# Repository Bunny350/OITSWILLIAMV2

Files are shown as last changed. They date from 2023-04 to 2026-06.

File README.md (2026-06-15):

<p align=center>
    <a>
        <picture>
  <source media="(prefers-color-scheme: dark)" srcset="https://raw.githubusercontent.com/Bunny350/OitswilliamV2/main/Media/Logo/2026/oitswilliamv2-2026-white-text-dark-bg.svg">
  <source media="(prefers-color-scheme: light)" srcset="https://raw.githubusercontent.com/Bunny350/OitswilliamV2/main/Media/Logo/2026/oitswilliamv2-2026.svg">
  OitswilliamV2
</picture>
    </a>
</p>

Welcome to the distant future.

# OitswilliamV2

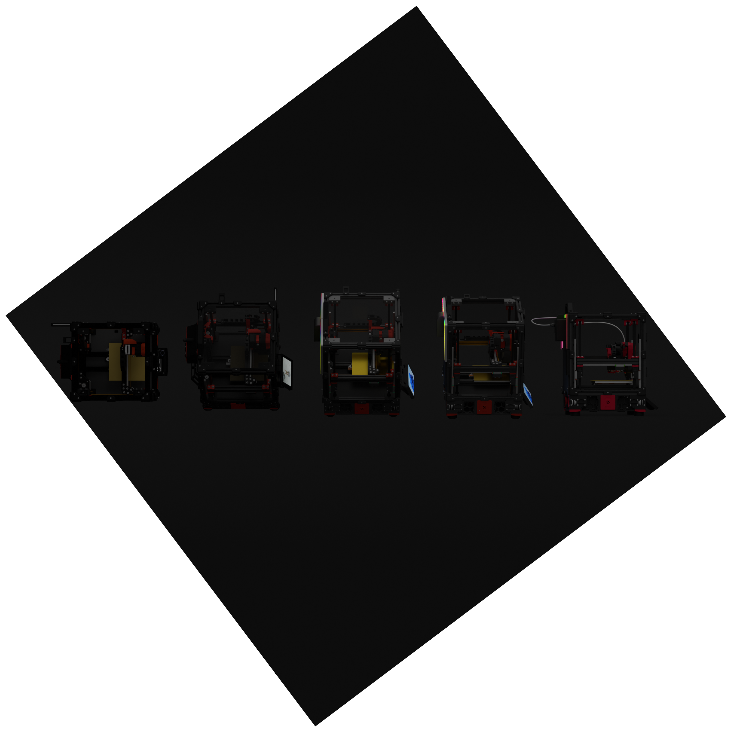
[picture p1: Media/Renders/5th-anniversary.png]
Various iterations of shrunk-down Voron 2 + OitswilliamV2 add-ons.


* Currently featured in V2.3347[^config-on-other-side]!

[View BOM](https://docs.google.com/spreadsheets/d/1hI7gKyXv_dqwRoAh5GxhNzBPyU9dn64bGJ1oHiKoa74/edit?usp=sharing)

OitswilliamV2 is a Voron 2 mod project with unique features, and sometimes breakthrough or stupidly insane features you will stop regretting slowly. It is modded by Oitswilliam Pang and the [original design](https://github.com/VoronDesign/Voron-2) is by the members of Voron Design.

This project is for those who already had a normal and big Voron printer (can be from friends or relatives), with the exception of original parts and skirts.

## Goal
The goal for this mod is:
* Make it unified,
* Make it safer to use,
* And make it intuitive for years to come.

## Feature development status

| Feature  | Status |
| --- | --- |
| Exhaust Lite Generation 2 | Released |
| RealEstate Generation 2 | Released |
| Tracker mount / AirTag mount G4 | Released |
| Tracker mount / Galaxy SmartTag2 mount G2 | Released |
| Replacement / 150mm build 60mm fan mount | Released |
| Replacement / Banger speaker skirts | Released |
| Electronics mounts / Replacement skirts made specifically for SBCs | Released |
| Electronics mounts / Replacement skirts made specifically for NUC PCs (12 Pro to 15 Pro) | Released |

## Features
This repository includes V2 150mm, which is basically Voron 2, but smaller. It includes skirts made for such printing dimensions.

### Using OitswilliamV2 Mod components

When using OitswilliamV2 mod components to modify the printer, you can take either one or more with:
* Sleek yet tiltable touchscreen mount called RealEstate.
    * Touch screen support after having OctoScreen / OctoDash (for OctoPrint users) or KlipperScreen (for Moonraker / lightweight WebUI users)
* Full DC input (no AC). (150mm mod only)
* Smaller version of chamber exhaust called Exhaust Lite.
* Zero limits, indefinite possibilities, through NUC.
* Installing Windows / Debian Linux SBC (single-board computer) or NUC requires replacing the display for the better experience.
* Flying colors (RGB LEDs) via Exhaust Lite.
* Webcam from the back facing at the build plate.
* Make the printer trackable through an item tracker.
* Modular vent port to exhaust hose.
* Some mods even extend to Voron Trident. See STLs Readme for explanation.

### Building from start

OitswilliamV2 is a mod for shrunk-down Voron 2.4 with 150x150x130mm build area except that can be a powerhouse of magical flying colors. Other features including:
* It has a DC power input and power output.
* Will have LED bars for users who are interested in putting "flying colors" in back panel.
* Panel clips can be printed in TPU, to prevent scratching on surfaces prone to scratching.

For the repository creator, it is because he originally did not have enough space to put a proper Voron 2.4.

Check out [parts printing Markdown file](https://github.com/Bunny350/OitswilliamV2/blob/For-Voron-2.4/Parts%20printing.md) on what mod parts should be printed based on your preference. It could entertain, or just be a printer.

#### Recommended BOM changes required when compared normal V2.4 with V2.4 150mm:
| Standard V2.4  | V2.4 150mm |
| --- | --- |
| Z chain - IGUS E2-15-10-028-0 Chain | X/Y chain - IGUS E2i-10-10-018-0 Chain |
| Z chain end - IGUS E2-150-10-12PZ Chain Ends | X/Y chain end - IGUS E2-100-10-12PZ Chain Ends |
| 2x SKR 1.3 | 1x BTT Octopus, FYSETC Spider or MKS Monster8 |

* Z chains should be replaced with X/Y chains due to off-distance towards left.
* Stripping 1kg of weight in such small printer requires usage of 4 Clockwork 1 motors (NEMA17 Motor 17HS08-1004S or equivalent) to replace Z axis stepper motors.

#### Recommended BOM changes required when compared normal V2.4 with the mod when build from start:
| Standard V2.4 recommended | V2.4 150mm + OitswilliamV2 Mod Project |
| --- | --- |
| Coroplast panels as bottom, back and Deck panels | Acrylic panels as bottom, back and Deck panels|
| Internal power supply | External / dedicated power supply |
| AC heated bed | 24V DC heated bed |
| AC input | 24V DC input |

## Kit promotion guidelines
If you want to sell the kits of this mod project, please call it "Voron 2.4 with OitswilliamV2 Mod" or related means that mentions Voron 2 and OitswilliamV2. Do not call it "Voron 2.4 enhanced version" or any other means.

## Questions
### How powerful is OitswilliamV2?
It's more powerful than the average home computers, at least on V2.3347. The only thing that's behind is a computer that has RTX 2060 (desktop) / RTX 2070 Mobile GPU and / or 12th generation Intel Core i7 desktop CPU. However that normally doesn't count if the printer's XY axes motors are not running on 48V power.
### Is 150mm an official spec size of Voron 2.4?
No. There are speculative reasons on why 150mm is not the spec size.
1. The spacing of the mounts between themselves needs to be changed, which means, like for example standard size (from 250mm to 350mm) has 150mm spacing between the bed mounts, but on a 150mm Voron 2.4, the bed mount needs to be narrower. Unless you have a router or a bench that can perfectly drill corners, the bed mount holes must be moved narrower in about half in order to make sure it is easily mounted.
2. Another reason is that one of the chain needs to be changed. Instead of using the chain intended for the Z axis, XY chain is used on the Z axis.
### This part is important, does Oitswilliam Pang Terms of Use apply to this project?
No, as it is licensed under the same license as the original Voron 2 project, or GPL-3.0. Oitswilliam Pang ToU does not apply to this repository.
### Can OitswilliamV2 be the first printer?
Despite it looks way too appealing that you could have indefinite possibilities with this machine, it is intended towards tinkerers. Users who are interested doing this should have a larger printer. Unless if fairytale is real, except that could never.

This project still requires the user to know how to build.
### Is this project suggested, built or vibe-designed by generative AI?
No, none at all, and generative AI can get out.

* Some people said with the help of 250mm spec is the best, this project may agree. Although right now most important parts (from the original and from this repo) are compatible and to be printed on a smaller printer, and then some other parts, except the bottom panel, can be printed within a 150mm print volume.

If you have built a shrunk-down or small printer first (i.e. V0, with or no mods, smaller than Spec V1 / VT, V2 or Switchwire, excluding Z height), you may need to build a bigger printer, or **ask someone or service** for your bigger projects.

For any other questions, you can visit [Oitswilliam Pang support](https://oitswilliam.com/support), where you can contact, email or join the groups for the mod packages, or [VORON Design Discord server](https://discord.gg/voron) and [VORON Forum](https://forum.vorondesign.com) on the original elements.

## Special Thanks
* Thanks to [VORON Design](https://github.com/VoronDesign) for the Voron 2 CAD model.
* The NUC decision is vaguely inspired by [NucDeck by CNCDan](https://github.com/dmcke5/NucDeck), Oitswilliam watched the video before his own research and final decision. 

[^config-on-other-side]: The configuration files for the following printers are not included in this repository, only organized, specific and cleaned-up. To get V2.3347's exact configuration files, you must be a follower of Oitswilliam Pang and then get follower-exclusive features through [this form](https://docs.google.com/forms/d/e/1FAIpQLSe9aEM7jyf0lV2PUAgOg0_tz9F7GI91byWFxUzvXsLlXambJA/viewform?usp=header). Other steps are provided from the form.

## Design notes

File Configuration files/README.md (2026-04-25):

# Configuration files
This folder contains mostly Klipper configuration files and non-Klipper configuration files stored in /Non-Klipper folder.

## Requirements for Non-Klipper configuration files
* This requires Adafruit CircuitPython firmware.
* For RealEstate display mount:
    * Please refer to page 44 of [RealEstate G2.1 assembly manual](https://github.com/Bunny350/OITSWILLIAMV2/blob/For-Voron-2.4/Manuals/realestate-generation-2-1-assembly-guide.pdf) on how to use these files.
    * Please refer to page 17 for wiring illustration or page 12 for wiring diagram.

## Other notes
* Only followers of Oitswilliam Pang from Facebook, Instagram and subscribers on YouTube can view and borrow Oitswilliam's printers' (V2.3347) current configurations. This folder holds cleaned-up configurations.

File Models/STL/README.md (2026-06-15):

This folder stores STLS of this project.
## Compatibility
Some of this mod supports both Voron Trident and Voron 2.4. However, this project is intended for Voron 2.4 with a modded spec.
| Mod name | Folder location | Voron Trident | Voron 2.4 |
| --- | --- | --- | ---|
| Exhaust Lite Generation 2 | Exhaust Lite | :heavy_check_mark: Fully supported |  :heavy_check_mark: Fully supported |
| ELG2 LED back | Exhaust Lite/LED Back | 150mm mod spec specific | 150mm mod spec specific |
| RealEstate Generation 2 | RealEstate | :heavy_check_mark: Fully supported | :heavy_check_mark: Fully supported |
| Tracker mount (AirTag and Galaxy SmartTag) | Tracker mount | :heavy_check_mark: Fully supported[^daretodeploy] | :heavy_check_mark: Fully supported[^daretodeploy] |
| Deck mounting brackets[^notea] | Replacement | :heavy_check_mark: Fully supported | :heavy_check_mark: Fully supported |
| Front side of 150mm mod skirt[^noteb] | Replacement/Skirt | :x: Not supported | 150mm mod spec only |
| Fan mounting skirt for 150mm mod[^notec] | Replacement | 150mm mod spec specific | 150mm mod spec specific |
| Bottom panel of the printer | Replacement/Bottom panel | 150mm mod spec specific | 150mm mod spec specific |
| 150mm mod SBC-specific skirt | Electronics mounts/Computer mounting/SBC | :x: Not supported | 150mm mod spec specific |
| 150mm mod NUC-specific skirt[^noted] | Electronics mounts/Computer mounting/NUC | :x: Not supported[^nointents] | 150mm mod spec specific |
| Condensed 60mm fan grill | Replacement | :heavy_check_mark: Fully supported |  :heavy_check_mark: Fully supported |

[^notea]: The part in question is called *din-rail-bypass-deck-mount-X4.stl*. These (being four of these parts) are used to mount the deck panel without the DIN rail being mounted with. It can be mounted with M3x8mm to M3x10mm BHCS / SHCS. This part is located in Replacements folder.
[^noteb]: This includes the following part names: *front-skirt-150mm-mod-left.stl* and *front-skirt-150mm-mod-right.stl*.
[^notec]: This part mounts one 60mm fan or some accessories into the printer. It uses the same mounting screws as the original. There are two variants for attaching the mount into the frame, *[base]150mm-60mm-fan-mount-m3x8.stl* which uses M3x8mm SHCS, but it seemed way too weak, so there is another variant called *[base]150mm-60mm-fan-mount-m3x12.stl* which requires M3x12mm SHCS on mounting to the frame.
[^noted]: Currently supports NUC 12 Pro to 15 Pro, but we have intent to make one that is made for NUC 16 Pro.

* Most mods for Voron 2.4 do support Voron Trident, but some parts need user testing.
* Most mods for Voron 2.4 do not support Voron 0, Voron 1.8, Voron Legacy or Voron Switchwire.

### <div id="nuc">NUC Mini PCs and SBCs</div>

OITSWILLIAMV2 mod now uses ASUS / Intel NUC PC which is inserted onto the back of the printer's skirt. This part only supports V2 in 150mm build size (mod). It used to support Morefine M6 with two mounting options (DIN rail mount or adhesive on the bottom) and universal (variant doesn't matter), but because of it's bad performance and compatibility, we have decided to discontinue them. OITSWILLIAMV2 also contains 150mm (mod) skirts that are made specifically for single-board computers such as Raspberry Pi, et cetera.
* For users who still want or repair mounts for Morefine M6, [the last CAD commit with such model](https://github.com/Bunny350/OITSWILLIAMV2/tree/df8fa697d1fd7cfa57b1f74a1fd6d7f7c9acae59/Models/CAD/VORON2.4-150mm) can still be accessed, and the STL models can be accessed [here](https://github.com/Bunny350/OITSWILLIAMV2/issues/4).

## Color guide
* If the part name does not have any brackets at the beginning you may use the printer's base color to print the part.
* [acc] - Printer accent color.
* [opaque] - Opaque color, it should block most of the glowing elements. It can be opaque base or accent color.
* [transparent] - Transparent color, it should allow the glow to pass-through and can be diffused. Transparent PETG / PC is recommended.
    * Transparent ABS can be used but seems rare in FFF 3D printing.

##  Printing guidelines
This section tells how to basically configure print settings.
Some parts require a bigger printer to print.
### Settings
These parts require ABS, PETG or PC to print.
Settings and parameters must be set to the following values:
* Layer height 0.2mm
* Layer width of 1.6mm (for 0.4mm nozzle) or 4 layer lines (for 0.4 / 0.6mm nozzle)
* Infill density of 40%, but,
    * On LED diffusers ([transparent]led-diffuser-(direction)-100-infill), the infill density must be 100%,
* Any slicers are welcome.
* Some inner parts such as grills requires modifiers to optimize printing performance.

[^daretodeploy]: This is best when showing off people at the 3D printer-related events, to prevent losing the printer. I know about MRRF, but I couldn't visit. Maybe in the near future I may do that.
[^nointents]: There is no intent in extending support to Trident, V0, et cetera, but there will be for Micron Plus.

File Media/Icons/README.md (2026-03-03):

# Icons
These are the icons made specifically for OitswilliamV2. These icons may not be used in assembly guides of their own.

| Icon | Artist |
| --- | --- |
| realestate-g2-display-s.svg | [Oitswilliam Pang](https://github.com/Bunny350) |
| v2-150mm-stealthburner.svg  | [Oitswilliam Pang](https://github.com/Bunny350) |

## Making new icons
Please refer to [2D drawings in Contributing Markdown document](https://github.com/Bunny350/OITSWILLIAMV2/blob/For-Voron-2.4/CONTRIBUTING.md) on making new icons for this project.

The icon must be in SVG, and must be simplified through your imagination.

### Simplification
To simplify the products for icons, it needs to:
* Have text removed,
* No small cutouts,
* Have complex geometries reduced.

## Passing icons to your *own* materials outside OitswilliamV2 project

It is recommended to credit our designs when passing these icons to your own materials. 

You may use the following phrase or related:

* *"Some icons" by "artist" in OitswilliamV2.*

For example, if there are icons *realestate-g2-display-s* and *v2-150mm-stealthburner* used, it will be written as *realestate-g2-display-s and v2-150mm-stealthburner by Oitswilliam Pang in OitswilliamV2.*

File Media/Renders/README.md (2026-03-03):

# Renders folder
This folder holds render images of Voron 2 150mm + OitswilliamV2 mod.

## Don't let generative AI companies train data out of these, thank you. Although it didn't help as these don't read disclaimers, certain licensing terms, certain copyright warnings or general warnings.

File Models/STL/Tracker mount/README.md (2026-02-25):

# Tracker mount
This folder contains tracker mount to Voron printers, for AirTag and Galaxy SmartTag2.
## IMPORTANT NOTE
**Do not use these for unwanted tracking. These parts are only intended to track printers that are installed with them.**

## Recommended materials
These parts are recommended to be printed in **ABS / ASA**. Other materials can be printed but the compliant design may not function properly, including but not limited to, requiring excessive force to secure or remove.

## Installation instructions
Please refer to the [assembly guide for both tracker mounts](https://github.com/Bunny350/OitswilliamV2/tree/For-Voron-2.4/Manuals/TRACKER-MOUNT-2026.pdf) for exact installation.
Insert the tracker to the main unit, then secure it with the bracket or nut. The assembled unit is then attached to the one of the skirt of the printer that has the unit mount installed.

## Removal and deactivation instructions
* Turn the unit counter-clockwise and then pull to remove it.
* For AirTag, unless the part is imperfect, the battery case can be removed without removing the bracket, otherwise, remove the bracket first, by turning the bracket counter-clockwise, and then remove that.
* For Galaxy SmartTag2, a SIM ejector tool is required. It can be made from the paper clip. Turn the nut counter-clockwise to remove it, and then use the SIM ejector tool to punch down in the hole that is placed at the back-middle of the silver ring of the tracker, and pull the battery tray.

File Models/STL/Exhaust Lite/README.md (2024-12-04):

## Directory printing guide for ELG2
This page shows what method you should use when choosing. Directories that are not in list must have all parts printed (excluding another directory in it).

### Legend: Parent / Child / Child / [Variants] ...

### Directories that need all parts in it printed:
* Filter cartridge
* LED Back (opaque visibilities)

### Directories that let you print either part by back panel thickness:

* Body unit / Exhaust spacer
* LED Back / [Back panel thickness (4 / 6mm)]

### Directories that let you print one of either part by back panel thickness and max cabling depth:

* Cable cover / [Back panel thickness (4 / 6mm)] / [Depth (10 / 15mm)]

### Directories that let you print one of either parts by screw type of coupler:

* Bowden coupler
	* Currently, one with runout sensor only supports 1/8" BSPP coupler.

### Directories that let you print one of either part by screw type:

* Unit cover

### Directories that let you print one of either part by whether should you embed a webcam to ELG2:

* Chamber cover

### Directories that let you print for one of either variant of webcam you mount, or not required if not installing it:

* Webcams

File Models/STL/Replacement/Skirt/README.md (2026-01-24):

# The skirt folder

This folder contains skirt parts intended to be placed on V2 in 150mm build volume.

## Side skirts
The side skirts (side_skirt_a_150_mesh.stl and side_skirt_b_150_mesh.stl) needs processing settings changed prior to print:

* Zero top and bottom layers
* 6 wall count, if using 0.4mm nozzle, or 2.4mm walls.
* Sparse infill density can be between 15% and 50%.
* You can choose what infill pattern that fits for you.
* Might as well adjust the infill direction in angle if you are not satisifed during preview before print. 

If the printer is going to be installed with banger speakers, then you may only print a pair, otherwise you may print two pairs.

## Front skirt
The front skirts (front-skirt-150mm-mod-left.stl and front-skirt-150mm-mod-right.stl) can follow the normal print settings, but it does not have any screws to hold, as it might otherwise weaken the part significantly. Because of this, I made a workaround where the front clips are attached to the bottom panel via screws instead of the multi-sided tape.

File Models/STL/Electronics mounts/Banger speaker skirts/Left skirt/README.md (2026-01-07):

This folder consists of two models that must be grouped and "merged".
## Printing guide
The normal part can be printed with the current settings, but the infill modifier must have its settings changed:
* There should not be top or bottom layers, you may set them to 0 / 0mm in both top and bottom layers.
* You may add or deduct one wall layer.
* Infill density must be between 25% to 50%.

## Setup guide on slicers

### UltiMaker Cura (with workaround)
Based of [How to merge and group models in UltiMaker Cura from UltiMaker Support](https://support.makerbot.com/s/article/1667411295122)
* Drop or open the STL models into the plate.
* Select **Merge Models**.
* Lay the model down and position the model to what you want.
* Ungroup the models.
* On the *infill modifier* of the part, modify its top and bottom layers by using **Per-model settings**.
    * Open the options by clicking **Select settings**.
    * Check the **Top/Bottom Thickness**. **Infill Density** and **Infill Pattern** is optional and will depend on what you want.
    * Change the Top/Botom Thickness to 0, and if you like to change the Infill Density, you may set it to somewhere between 25% to 50%, depending on what you want.
* You may do the same for the other part.
* The part can be sliced and printed.

### PrusaSlicer, et cetera, including Bambu Studio
**You must be at least in advanced mode in order to do so.**
* Drop or open either STL or 3MF models, for PrusaSlicer and not BambuStudio, you may open the 3MF model. It must be placing both models in a single drop per folder.
* It will warn that there are multiple parts while trying to load, Choose **Yes** as these are intended so.
* 
**This section is used for PrusaSlicer users if the infill modifier is not ready, or has top / bottom layers.**

Based of [Modifier meshes from Prusa Knowledge Base](https://help.prusa3d.com/article/modifiers_1767#modifier-meshes).
* Select the infill modifier of the part through the object menu, then click the edit cogwheel next to the part name or right-click on the part name.
* It will pop up the menu, select **layers and perimeters**. You can optionally add **infill** as well.
* Change the infill modifier top and bottom layers to 0, perimeter may also be set to 0, if one of the mesh is turned into top or bottom layer.
* You can optionally change the sparse infill density of such part, you may set it somewhere between 25% to 50%, you can also change its infill pattern to something you like, such as honeycomb.

**This section is specific to BambuStudio.**

Based of [Object level parameters from Bambu Lab Wiki](https://wiki.bambulab.com/en/software/bambu-studio/how-to-set-slicing-parameters#object-level-parameters)
* After importing, toggle the process to **objects**.
* Select the mesh modifier *in the process menu*.
* In the strength section for the infill modifier, set both **top shell layers** and **bottom shell layers** to 0.
* You can optionally change the sparse infill density of such part, you may set it somewhere between 25% to 50%, you can also change its infill pattern to something you like, such as honeycomb.

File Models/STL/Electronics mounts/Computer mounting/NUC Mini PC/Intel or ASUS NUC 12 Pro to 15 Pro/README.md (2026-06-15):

This folder consists of necessary parts for mounting ASUS / Intel NUC 12 Pro to 15 Pro into Voron 2 in 150mm mod.

## Requirements
[View BOM, you may select NUC Mini PC when browsing.](https://docs.google.com/spreadsheets/d/1hI7gKyXv_dqwRoAh5GxhNzBPyU9dn64bGJ1oHiKoa74/edit?usp=sharing)

### In a nutshell
* Base color of the printer,
* ASUS / Intel NUC 12 Pro, 13 Pro, 14 Pro or 15 Pro, **slim version**
    * Other versions, including the tall version, *Pro Plus*, *Pro AI* or any other variants do not fit. In addition, these printed parts heavily rely on such models of NUC with the metal shell.

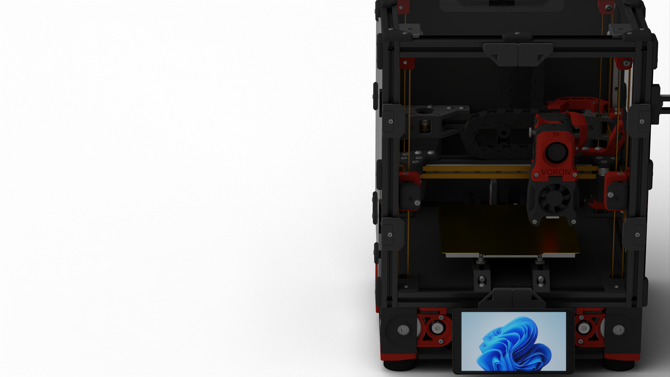
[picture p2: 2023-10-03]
Media/Renders/v2-150mm-top-side-cam-off-righthand-2K.png

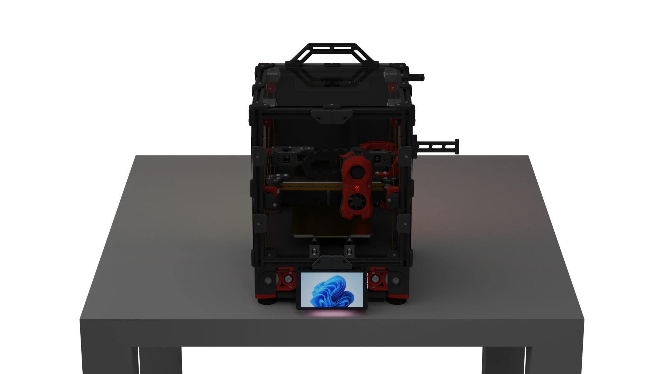
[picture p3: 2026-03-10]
Media/Renders/v2-150mm-oitswilliamv2-mod-top-bottom.png

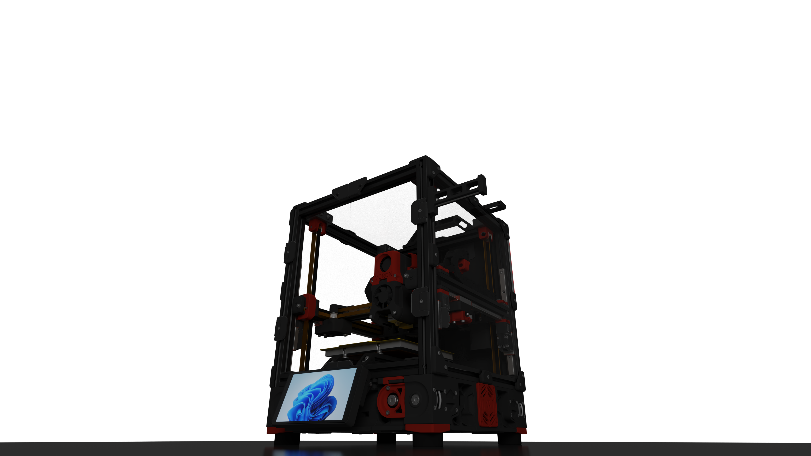
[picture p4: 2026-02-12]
Media/Renders/bottom-front-side-render.png

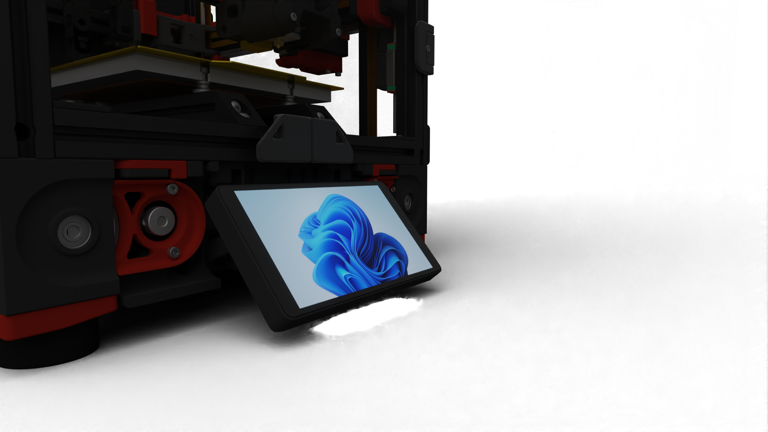
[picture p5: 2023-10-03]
Media/Renders/realestate2-side.png

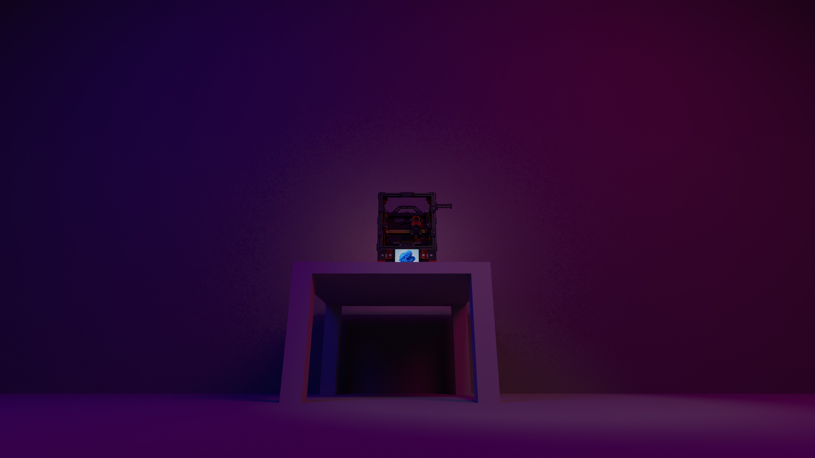
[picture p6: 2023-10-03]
Media/Renders/sick machine-2K.jpg

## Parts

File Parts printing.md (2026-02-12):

# Parts printing
This page guides users on printing required parts.

## I want it to live, entertain everyone, be like a boombox and treat it like a computer
The required parts are:
* RealEstate G2
* NUC-specific skirt
* Banger speakers
* 2x 60mm fan mount for 150mm Voron printers ([STL](https://github.com/Bunny350/OITSWILLIAMV2/tree/For-Voron-2.4/Models/STL/Replacement)) ([CAD](https://github.com/Bunny350/OITSWILLIAMV2/tree/For-Voron-2.4/Models/CAD/VORON2.4-150mm/150mm%20mod%2060mm%20fan%20mount))
* 1 pair of normal side skirts ([STL](https://github.com/Bunny350/OITSWILLIAMV2/tree/For-Voron-2.4/Models/STL/Replacement/Skirt))
* Tracker mounting is generally recommended ([STL](https://github.com/Bunny350/OITSWILLIAMV2/tree/For-Voron-2.4/Models/STL/Tracker%20mount)) ([CAD](https://github.com/Bunny350/OITSWILLIAMV2/tree/For-Voron-2.4/Models/CAD/Tracker%20mount))

## I don't care about making it an enthusiastic computer, I've just want it to print, follow as many components as the original, but small
The required parts are:
* SBC-specific skirt ([STL](https://github.com/Bunny350/OITSWILLIAMV2/tree/For-Voron-2.4/Models/STL/Electronics%20mounts/Computer%20mounting/SBC)) ([CAD](https://github.com/Bunny350/OITSWILLIAMV2/tree/For-Voron-2.4/Models/CAD/VORON2.4-150mm/SBC-specific))
* 2x 60mm fan mount for 150mm Voron printers ([STL](https://github.com/Bunny350/OITSWILLIAMV2/tree/For-Voron-2.4/Models/STL/Replacement)) ([CAD](https://github.com/Bunny350/OITSWILLIAMV2/tree/For-Voron-2.4/Models/CAD/VORON2.4-150mm/150mm%20mod%2060mm%20fan%20mount))
* 2 pairs of normal side skirts ([STL](https://github.com/Bunny350/OITSWILLIAMV2/tree/For-Voron-2.4/Models/STL/Replacement/Skirt))
* Tracker mounting is generally recommended ([STL](https://github.com/Bunny350/OITSWILLIAMV2/tree/For-Voron-2.4/Models/STL/Tracker%20mount)) ([CAD](https://github.com/Bunny350/OITSWILLIAMV2/tree/For-Voron-2.4/Models/CAD/Tracker%20mount))

## Required spares
This mod requires a dedicated / external power supply, of:
* At least 300W for one with NUC inside,
* Or at least 200W for one with SBC.

## Procedure
This mod may intersect with the original assembly manuals: Voron 2 (2.4r2), Stealthburner, Tap. Please check this if you are building from start to finish.

* The mod may not use DIN-based electronics mounting, especially where such may conflict with NUC skirt.
* This mod recommends DC-powered bed, which removes the requirement of solid state relay (SSR).
* Voron 2 assembly manual from start to page 146,
* Voron Stealthburner assembly manual, from start to page 58, if using such tool head,
* Voron Tap assembly manual, if using such upgrade, otherwise proceed from page 59 to 67 of Stealthburner manual (if using such tool head),
* Pages 148 and 149 of Voron 2 assembly manual, 
* OitswilliamV2 NUC skirt, from start to page 25, if using NUC, or original assembly manual from pages 150 to 152 if using SBC,
* Pages 158 to 161 of Voron 2 assembly manual, if not using Voron Tap upgrade,
* Pages 162 to 164 of Voron 2 assembly manual,
* Pages 180 to 209 of Voron 2 assembly manual, AC part may be excempted,
* Pages 210 to 237 of Voron 2 assembly manual,
    * Pages 211, 214 to 216, and 220 to 221 contains monochrome LCD display,
    * If you are switching to RealEstate display, these sections need to be ignored and then referred to OitswilliamV2 RealEstate display assembly manual,
    * Item tracker mounting manual, if installing an item tracker,
    * The skirt mounting part of OitswilliamV2 NUC skirt, from pages 26 to 28, if already using NUC,
* Pages 238 to 249 of Voron 2 assembly manual, if using the original enclosing,
* Pages 250 to the end of Voron 2 assembly manual.

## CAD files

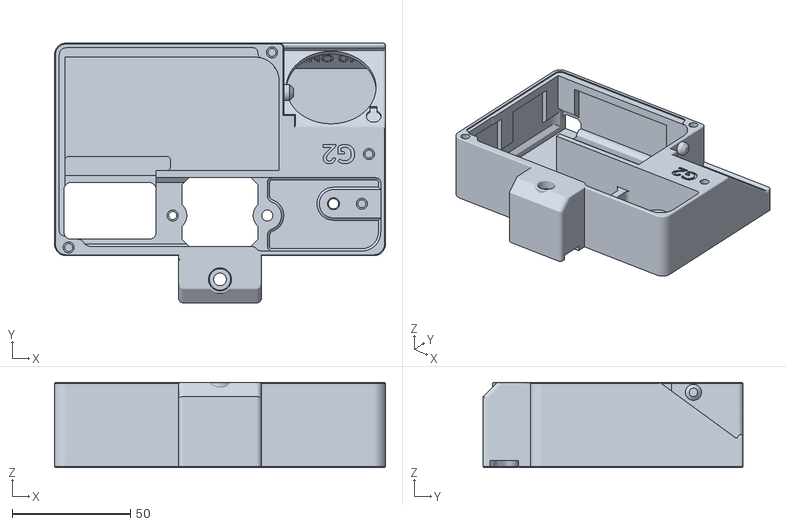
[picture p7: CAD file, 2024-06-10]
Models/STL/Exhaust Lite/Body unit/main-body.stl
140.0 x 110.0 x 36.0

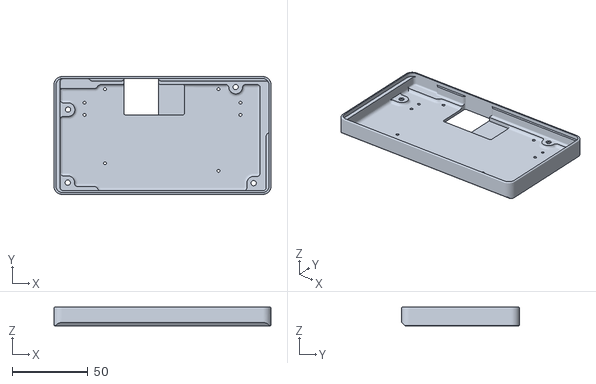
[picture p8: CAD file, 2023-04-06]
Models/STL/RealEstate/Main screen/main-screen-mount-waveshare-5.5-inch-amoled.stl
143.4 x 77.8 x 12.4

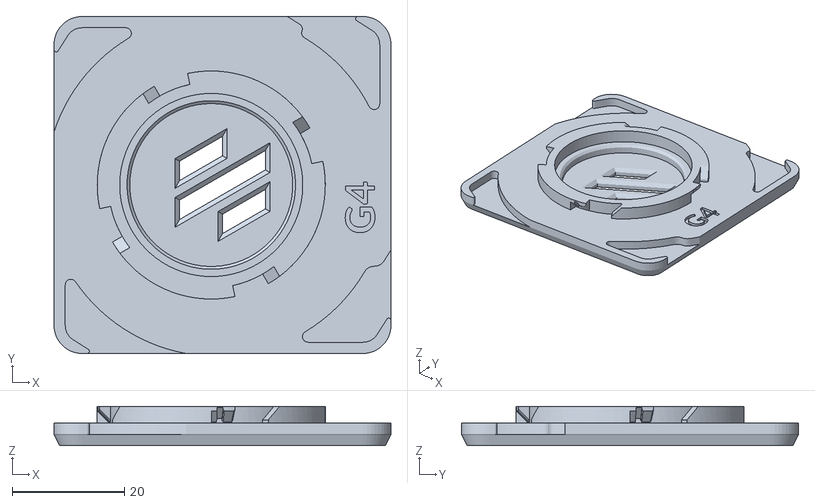
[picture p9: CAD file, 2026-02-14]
Models/STL/Tracker mount/AirTag/[acc]tracket-mount-airtag-main-g4.stl
60.0 x 60.0 x 7.00

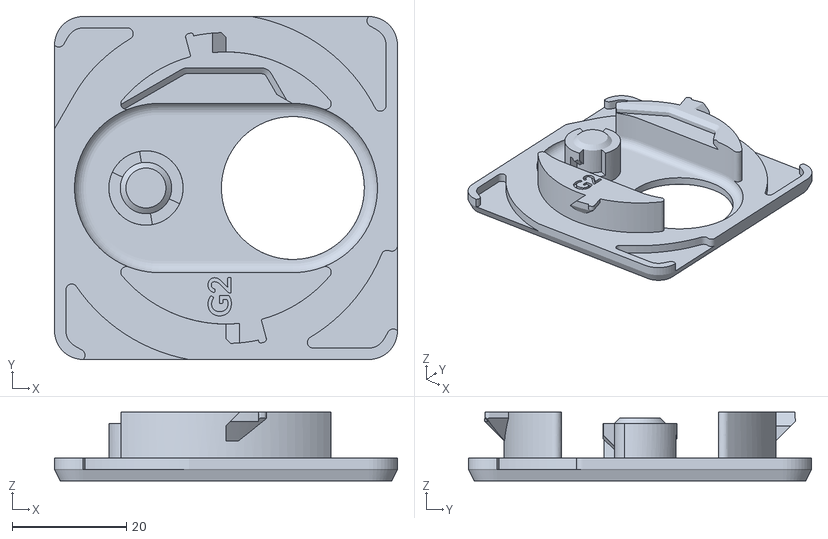
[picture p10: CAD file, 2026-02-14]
Models/STL/Tracker mount/Galaxy SmartTag2/[acc]tracket-mount-smarttag-main-g2.stl
60.0 x 60.0 x 12.0

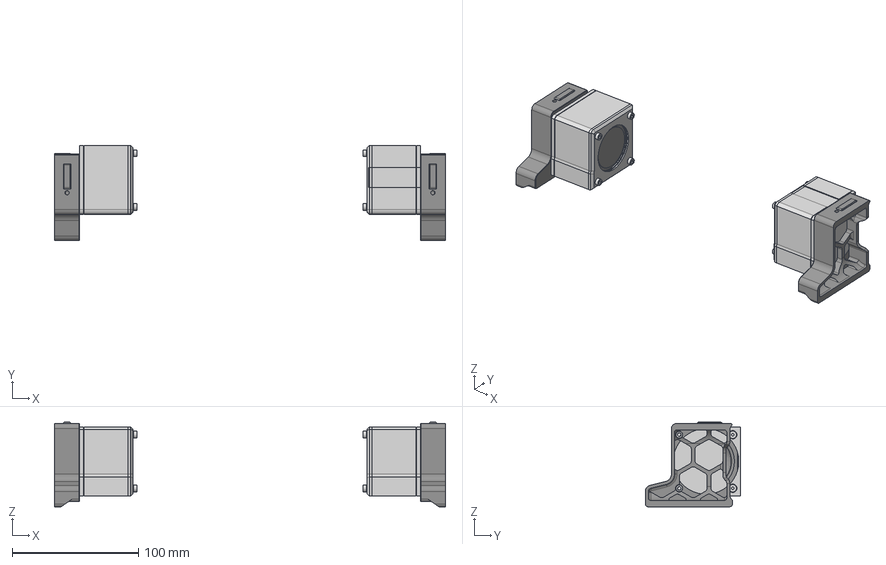
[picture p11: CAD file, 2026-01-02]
Models/CAD/Banger speaker skirts/banger speaker skirts on v2.step
310.0 x 75.6 x 67.0 mm
left side skirt infill mesh modifier
side_skirt_150_speaker_left
speaker unit
M3x6 FHCS v1 x 2
M3x8 SHCS x 6
M3 Threaded Insert x 8
right side skirt infill mesh modifier(Mirror)
side_skirt_150_speaker_right
speaker unit(Mirror)
M3x6 FHCS v1_1 x 2
M3x8 SHCS(Mirror) x 6
M3 Threaded Insert(Mirror) x 8

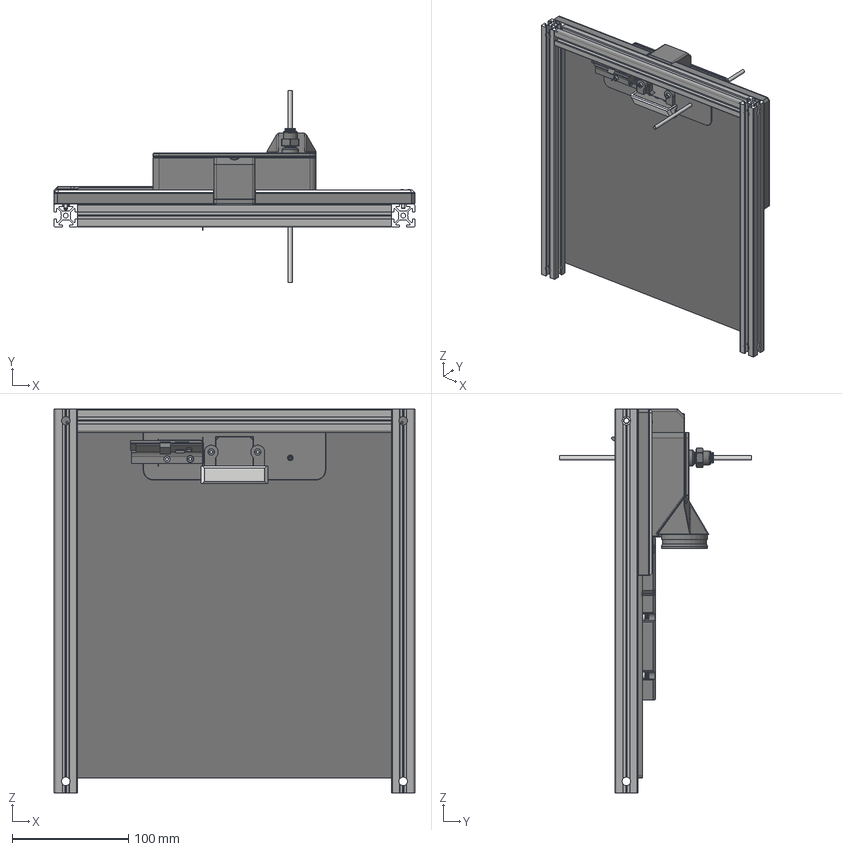
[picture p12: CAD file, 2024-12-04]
Models/CAD/Exhaust Lite/exhaust-lite-gen2 v40.step
310.0 x 165.4 x 330.1 mm
M2x10 Self-tapping Screw (3) x 12
led strip (READ MANUAL FOR QUANTITY)
M3x6 BHCS x 14
diffuser-6mm
ov5640-mount-back
ov5640-front-face
M3x8 SHCS (15) x 4
mini-webcam-backside
mini-webcam-cover
hardware (4)
exhaust-lite-chamber-cover-webcam
M3 Threaded Insert (69) x 9
cover-shcs
cover-bhcs
main-body
M3x20 SHCS (15)
M5x40 SHCS (5)
filter pieces
BSP Bowden Connector v1 (1)
pc4-m6-adapter
8-1-bspp-adap-runout
MR85 Bearing x 2
Omron D2F Microswitch
M5x30 BHCS (4)
filament dummy
40x40x10 DC Fan
6x3 magnet (1)
exhaust-lite-chamber-cover
M3x8 SHCS x 2
6x3 magnet
M3x16 SHCS (4) x 2
led strip (READ MANUAL FOR QUANTITY) (1)
M3x10 FHCS (5) x 2
spliced bowden tube

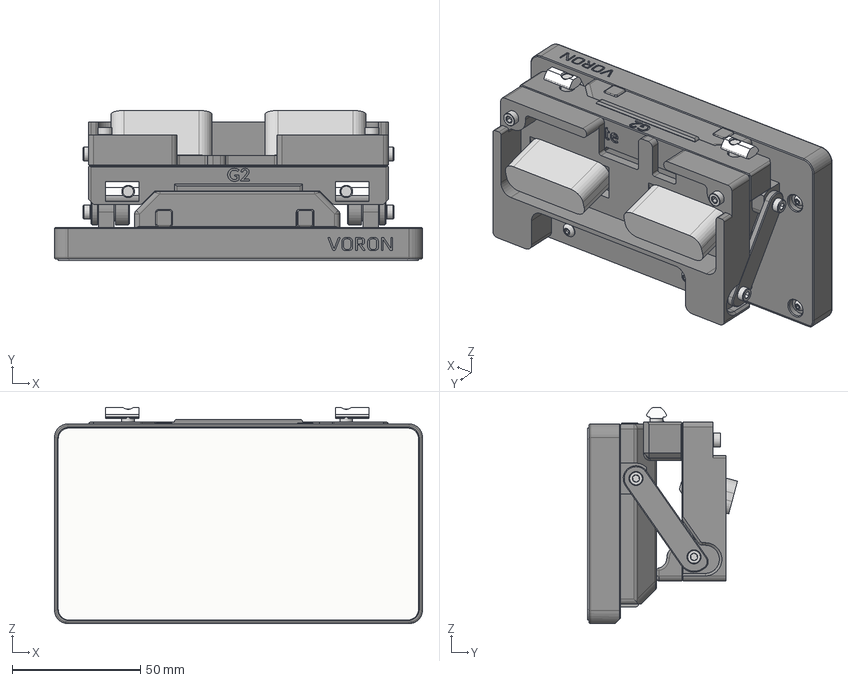
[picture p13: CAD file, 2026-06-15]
Models/CAD/RealEstate/realestate 2.step
143.4 x 58.5 x 84.3 mm
glass front
main display panel
92095A456_NO THREADS x 4
KW10 Microswitch (3)
hatch
hardware
hardware (1)
94180A331_NO THREADS_Tapered Heat-Set Inserts for Plastic x 4
91292A114_18-8 Stainless Steel Socket Head Screw(Mirror) x 2
94180A331_NO THREADS_Tapered Heat-Set Inserts for Plastic(Mirror) x 2
91292A114_18-8 Stainless Steel Socket Head Screw x 2
teflon-tube x 2
94209A315_NO THREADS x 8
6x3mm magnets x 2
92095A179_NO THREADS x 6
91290A120_NO THREADS_Alloy Steel Socket Head Screw x 2
M5x10 BHCS (15) x 2
2020 Drop-in T-nut, M5 (10) x 2

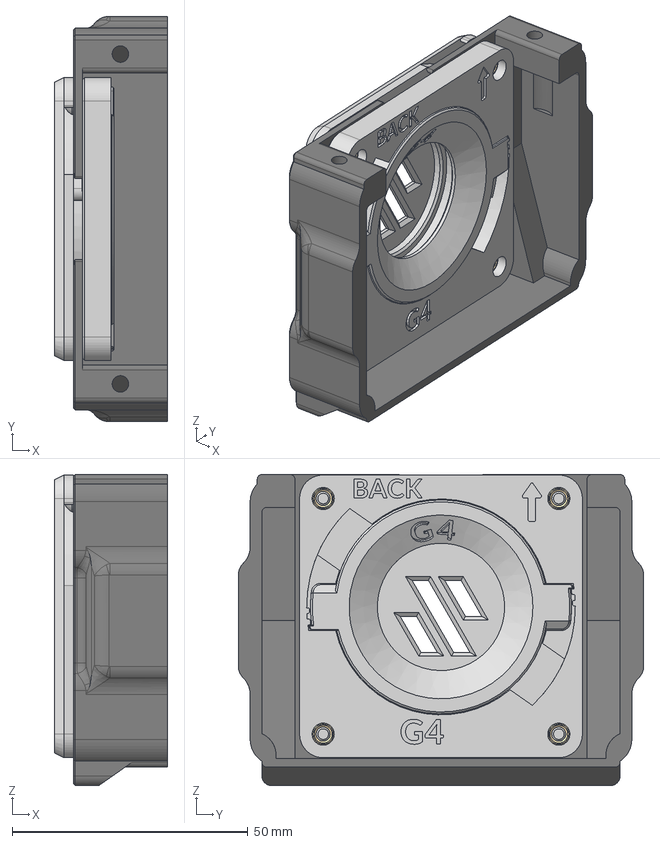
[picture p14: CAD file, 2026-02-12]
Models/CAD/Tracker mount/AirTag/oitswilliamv2 2.4r2 tracker mount (airtag) g4.step
24.0 x 86.0 x 66.0 mm
main
97763A812_NO THREADS_18-8 Stainless Steel Button Head Hex Drive Screw s x 4
M3 Threaded Insert x 4
reference materials

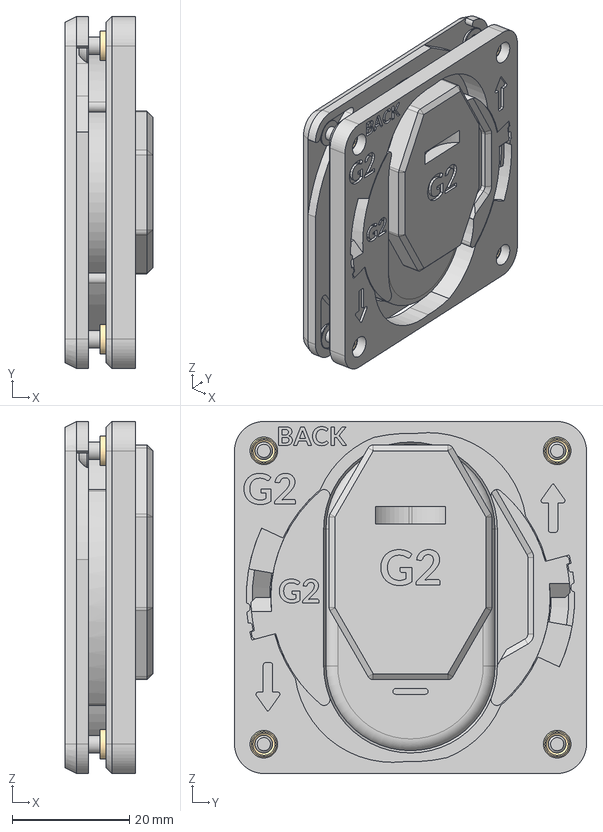
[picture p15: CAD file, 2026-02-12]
Models/CAD/Tracker mount/Galaxy SmartTag2/oitswilliamv2 2.4r2 tracker mount (smarttag) g2.step
15.0 x 60.0 x 60.0 mm
main
[raw]tracker
97763A812_NO THREADS_18-8 Stainless Steel Button Head Hex Drive Screw s x 4
M3 Threaded Insert x 4

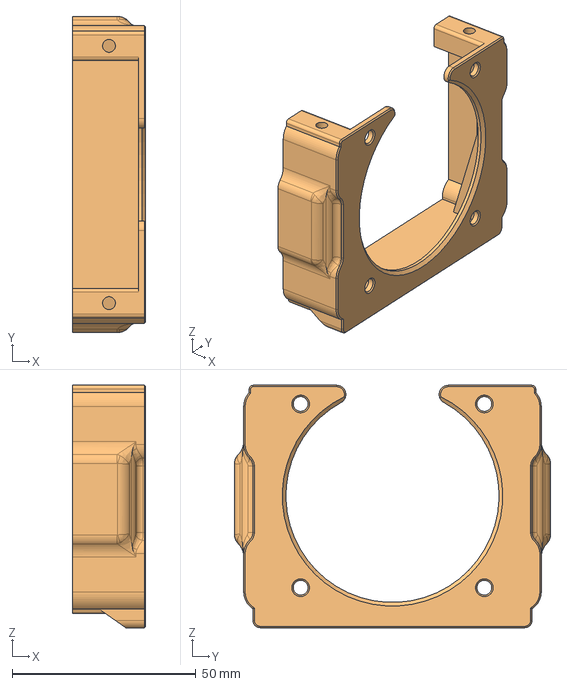
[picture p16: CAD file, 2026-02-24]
Models/CAD/VORON2.4-150mm/150mm mod 60mm fan mount/60mm-Fan-mount-150mm-mod.step
20.0 x 86.0 x 66.0 mm
150mm 60mm fan mount m3x8
150mm 60mm fan mount m3x12

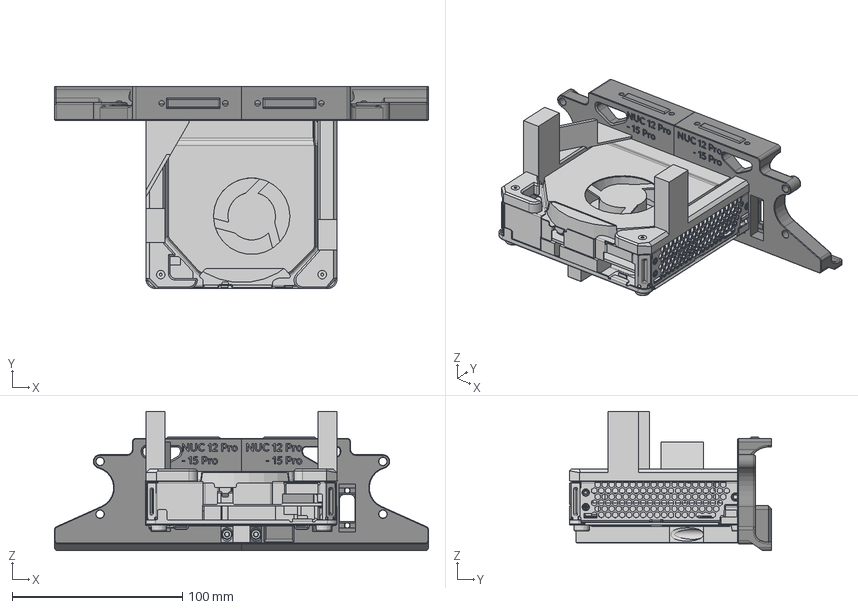
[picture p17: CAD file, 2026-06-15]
Models/CAD/VORON2.4-150mm/NUC-specific/nuc 14 15 in v2.step
220.0 x 119.1 x 82.0 mm
BKT_COVER_TOP_S_RV_CM_A2
STD_COVER_TOP_BKT_RV_CM x 4
MYLAR_K-LOCK-S_NUC_RV_CM x 2
SPONGE_POW_BTN_RUBBER_NUC_RV_CM
BKT_BOT_COVER_NUC14R3K
STD_BTM_THM_CU_S_NUC_RV_CM x 2
STD_VESA_BKT_S_NUC_LC x 2
STD_LATCH_BTM_COVER_RV_CM
PLS_BTM_LATCH_RV_CM
NUT-M2XL2-OD3
BKT_BTM_HOOK_RV_CM_MIR
SCREW-M2-L3-D5-H0_5 x 3
SPRING_RV_CM
PLS_LATCH_LOCK_COVER_BOT_CON
PLS_RING_LATCH_LOCK_BOT_CON
AL_FOIL_NUC14R3K x 4
MYLAR_FOIL_NUC14R3K x 4
RUBBER_SSD_CONN_S_NUC_LC
RUBBER_FOOT_NUC14R3 x 4
RUBBER_DIMM_RV_CM
back_skirt_nuc_12to15_pro_right
[NOT PRINTABLE]
reinforcement_stud_bottom_nuc_12to15_pro
reinforcement stud top - for within nuc 12 to 15 pro
M3 Threaded Insert x 4
91294A018_NO THREADS_Black-Oxide Alloy Steel Hex Drive Flat Head Scre w x 2
91290A123_NO THREADS_Alloy Steel Socket Head Screw x 4
vesa mount screw x 2
96367A180_NO THREADS_High-Strength High-Temperature PEEK Screw x 4

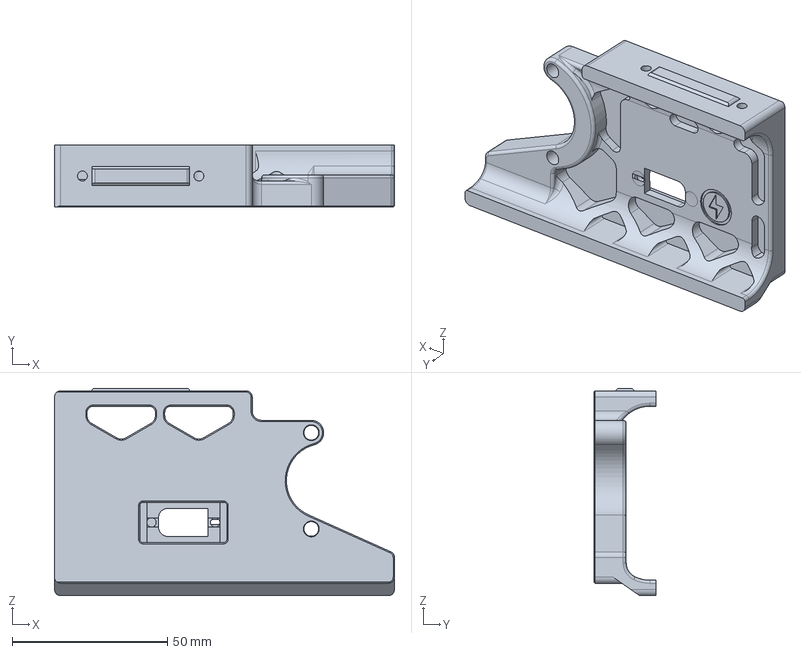
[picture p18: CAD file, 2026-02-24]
Models/CAD/VORON2.4-150mm/SBC-specific/Lefthand/[lefthand]power-inlet-dc-xt60-sbc.step
109.5 x 20.0 x 66.8 mm

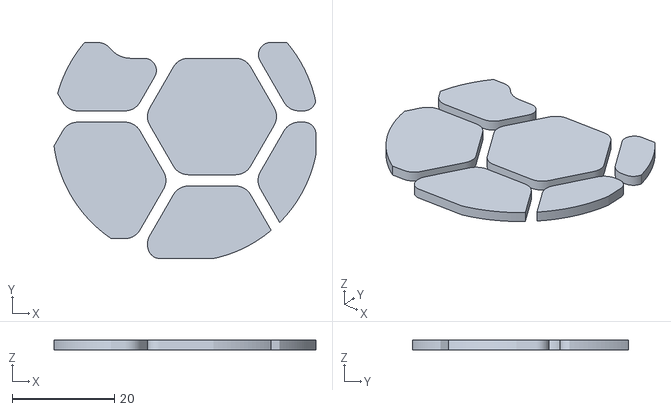
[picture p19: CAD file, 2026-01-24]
Models/STL/Electronics mounts/Banger speaker skirts/Left skirt/left side skirt infill mesh modifier.stl
51.3 x 42.3 x 2.00

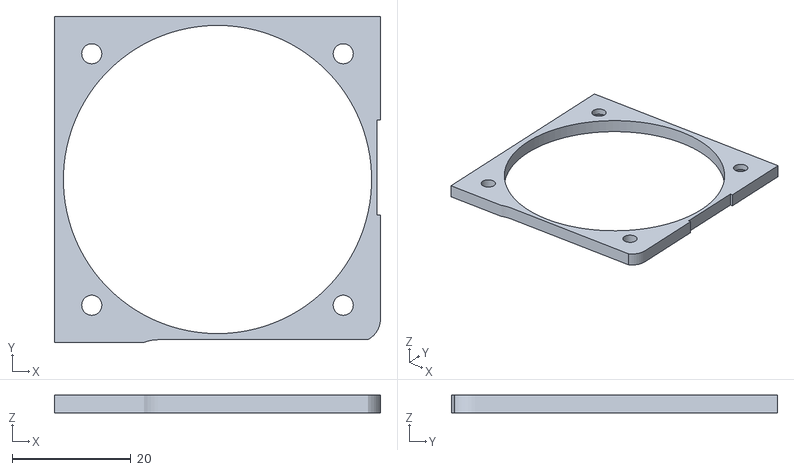
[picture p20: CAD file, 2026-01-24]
Models/STL/Electronics mounts/Banger speaker skirts/right_speaker_unit_bracket.stl
55.0 x 55.0 x 3.00

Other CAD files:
Models/CAD/VORON2.4-150mm/SBC-specific/Righthand/v2-150mm-panel-mount-usb v3.step
Models/STL/Electronics mounts/Banger speaker skirts/Right skirt/right side skirt infill mesh modifier.stl
Models/STL/Electronics mounts/Computer mounting/NUC Mini PC/Intel or ASUS NUC 12 Pro to 15 Pro/reinforcement_stud_top_left_nuc_12to15_pro.stl
Models/STL/Electronics mounts/Computer mounting/NUC Mini PC/Intel or ASUS NUC 12 Pro to 15 Pro/Supports required/back_skirt_nuc_12to15_pro_right.stl
Models/CAD/Banger speaker skirts/banger speaker skirts on v2.f3d
Models/CAD/Exhaust Lite/exhaust-lite-gen2.f3d
Models/CAD/RealEstate/realestate 2.f3d
Models/CAD/Tracker mount/AirTag/oitswilliamv2 2.4r2 tracker mount (airtag) g4.f3d
Models/CAD/Tracker mount/Galaxy SmartTag2/oitswilliamv2 2.4r2 tracker mount (smarttag) g2.f3d
Models/CAD/VORON2.4-150mm/150mm mod 60mm fan mount/60mm-Fan-mount-150mm-mod.f3d
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

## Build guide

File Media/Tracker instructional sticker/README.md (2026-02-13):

# Tracker instructional sticker
This folder contains SVG vector and PNG raster image files of the instructional stickers on how to access the tracker's owner in case if it was marked lost.

* For the PDF version, please refer to [Models/STL/Tracker mount/TRACKER-COMMON-FOR-VORON-ready-to-print.pdf](https://github.com/Bunny350/OitswilliamV2/tree/For-Voron-2.4/Models/STL/Tracker%20mount/TRACKER-COMMON-FOR-VORON-ready-to-print.pdf).

## Requirements
* Printable sticker paper.
    * "Printable" should suggest that it is compatible with normal inkjet printer.
* PDF version recommends 4x6", and may only be used for hand-cut stickers.
### Edge cutting
* For hand-cutting, scissors or utility knife,
* For cutting machine users (i.e. Cricut cutting machines or Bambu Lab H2 series), please make sure the following conditions be meet:
    * **Set both width and height to 4cm (40mm),**
    * **Only edges be cut.**
        * PNG version is made as an attempt to make print-then-cut procedure simple, at least for Bambu Suite. If the SVG version of such sticker tries to have text or icons cut, then you may try using the PNG version.

## Contributions and modifications
* Modifications are generally done through SVG vector images. It is not recommended to modify PNG raster images and instead should be exported from SVG.
### Publishing guideline
* To publish own tracker mount instruction to this repository, an SVG file (with no raster or unoptimized vector points) is required, while the PNG in 7500DPI (11811px in both width and height) is advised in-conjunction with SVG.
#### Special instructions for PNG version
* When being exported, be sure to remove the black edge which is the cutout before exporting.

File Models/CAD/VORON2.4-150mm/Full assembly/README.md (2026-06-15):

This folder contains a full assembly of Voron 2 in 150mm build volume and mods + upgrades that empower it.

## You may use this model for:
* Evaluation,
* Renderings,
* Use it whenever the instruction manuals are not clear.

You may not use this model for AI-generated or -remixed media, although this is just an advisory and we can only warn you for doing that (cannot ban).

## Included mods
* RealEstate G2
* Exhaust Lite G2 with camera
* NUC-specific skirt
* AirTag tracker mount G4

## Included upgrades
* [Voron Tap](https://github.com/VoronDesign/Voron-Tap)

## [The f3d file was all-of-a-sudden doubled, even if nothing changed, but just exported today.](https://www.facebook.com/share/p/1Hoa8yiPeh/)

## Why is the STEP CAD file compressed?
This is because the STEP file itself is 151.9MB, which is bigger than usually allowed per-file size. The compressed file is just around 28MB. And the compressed file should **not be locked with a password**, otherwise **do not access it**.

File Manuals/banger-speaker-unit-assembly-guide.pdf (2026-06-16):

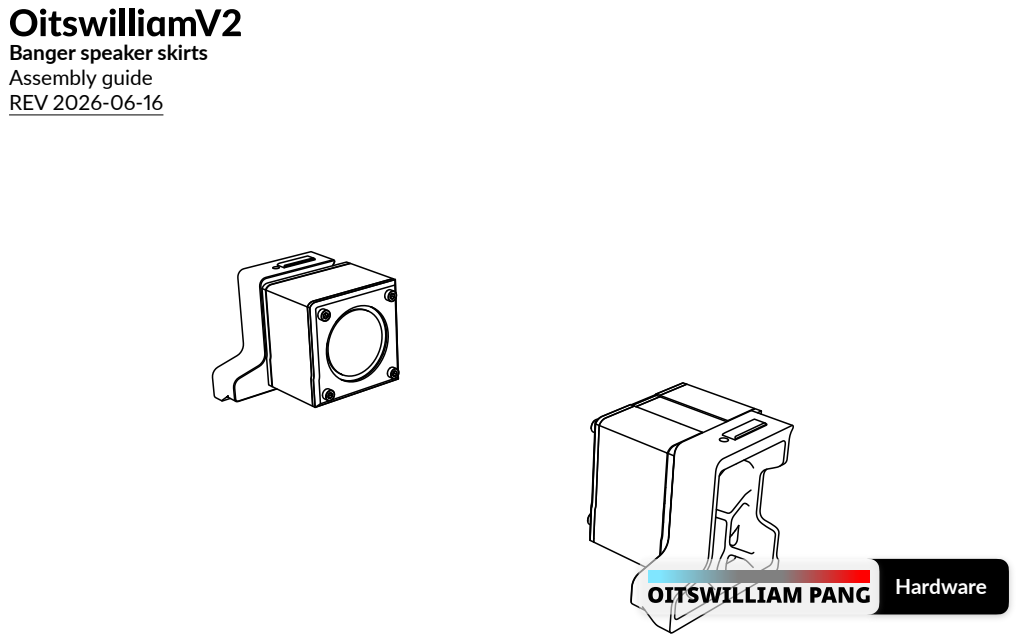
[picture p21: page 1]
Hardware

Banger speaker skirts
Assembly guide
REV 2026-06-16

2
Contents • Before getting started • Speaker wiring • Assembly • Exploded view • Detailed assembly • Software configuration

3
5
6

7
12

3

# Before getting started

You are about to read the manual of banger speaker skirts. This manual details about it and assembly of such speakers.
Warning
Danger: unless if it only runs on DC and only has a DC input, otherwise risk of electric shock
- Even though you can build with this mod from start, if you want to wire, or re-wire, you need to make sure and check that the mains is unplugged.
- Failure doing so which is unplugging the mains power may cause electrocution or even death.
- When in doubt, please don't touch the wires connected to the power supply or SSR.
Other notes
- There are two parts of model on each side of the skirts, these being the main part and the modifier. The modifier is used for adding the mesh on the part where it has ventilation or speaker cutouts. Please visit the parts' Readme file on how to prepare these.
- The righthand side of the speaker has another notch that is located at the top, whereas the lefthand side doesn't. This indicates the side and is used for alignment. If the righthand side parts are attached to the lefthand sides, or vice versa, it will be an obvious telltale sign that is incorrect. The box units contain two letters that indicate their sides.
- For their abbreviations, LH means lefthand side and RH means righthand side.
About the banger speakers
This mod adds speakers that sound as loud as it gets, with 30mm radiators to improve bass. It is mounted to Voron 2 150mm (mod). However users can access the CAD model of such model to attach them to other units. Users can install sound extension written by Al Williams to Klippy extra or use aplay command via Klipper Gcode Shell, or just become usable whether the machine becomes a PC.

4
Contribution
This mod is a part of OitswilliamV2 mod project through GitHub. You can visit, contribute and report new issues here. (https://github.com/Bunny350/OITSWILLIAMV2/)
Technical support
You can contact Oitswilliam here, (http://oitswilliam.com/support) or if the issue is not related to OitswilliamV2 mod, you may visit Voron forum or its Discord server.
Guide and legend
- - raw material
- - highlighted material
- - printed material, as this part is simple, the printed parts may be color-coded.

Part printing
The parts of this model can be printed in the base color of the printer. Bold text indicates the recommended value and italic text indicates on what setting / value it needs to set.

Material

Model
model.stl / model.3mf

Material

FDM / FFF or SLS | Print material: ABS, ASA or PA12, prohibits PLA.
Layer height of 0.2mm, initial layer height can be 0.2mm or higher. | Nozzle and extrusion width must be forced 0.4mm; if using 0.4mm nozzle
1.6mm wall width, or 4 wall counts. | Infill must be at least 40%, except on the infill modifiers.
At least 4 solid bottom and top layers, except on the infill modifiers. | The best print speed is up to 120mm/s. The speed might be reduced by the hot end flow rate.
Supports are recommended for main skirt parts. Use tree or organic supports if available. | Other settings might be depended on your printer. Follow it's warnings for proper handling.

5

# Speaker wiring

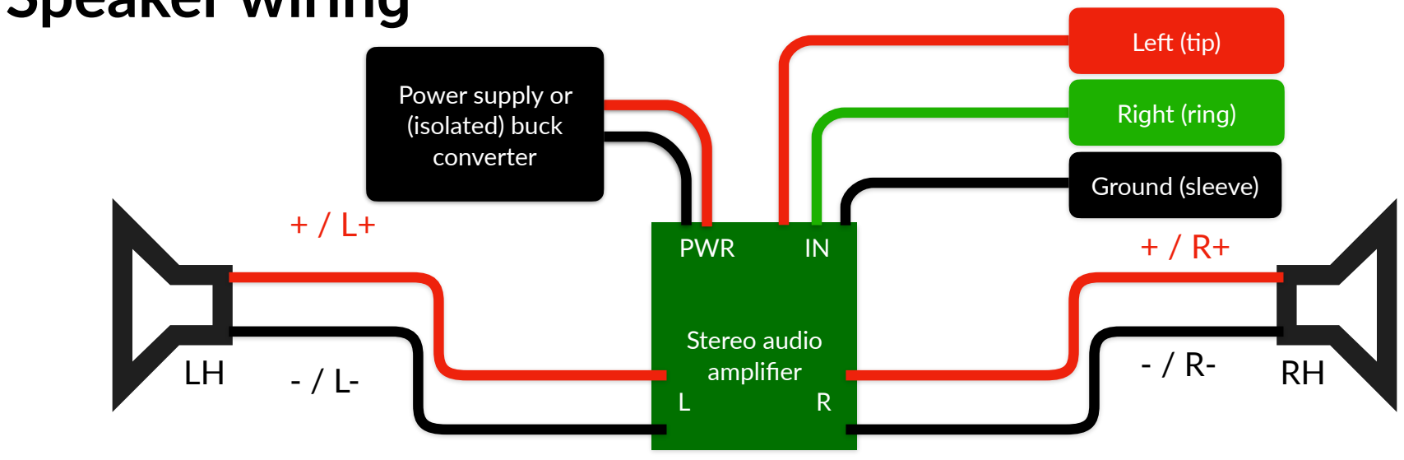
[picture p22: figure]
PWR; Stereo audio amplifier; Left (tip); Right (ring); Ground (sleeve); Power supply or (isolated) buck converter

- Note that the speaker wire polarity must be matched in order to function correctly, and should not be reversed.
- The power requirements for the amplifiers are different, some of them accept 5V, while others accept 12V or 24V.
- If the speakers did not have tails of wires, you may make them yourself. The wire length should be at least 250mm per connection, totaling 1000mm. (On bigger machines the length may be added more)
- The wiring colors for the analog TRS plug may be different, because of this, you may use a multimeter to check whether the wire and the jack match.
- For left (tip), it may use red or blue, for right (ring), it may use green, red or white and for grounding (sleeve) it may be either exposed, or covered with green or black insulation.
- After done wiring and testing, you may unplug them, and prepare them for installation to the printer.

# Assembly

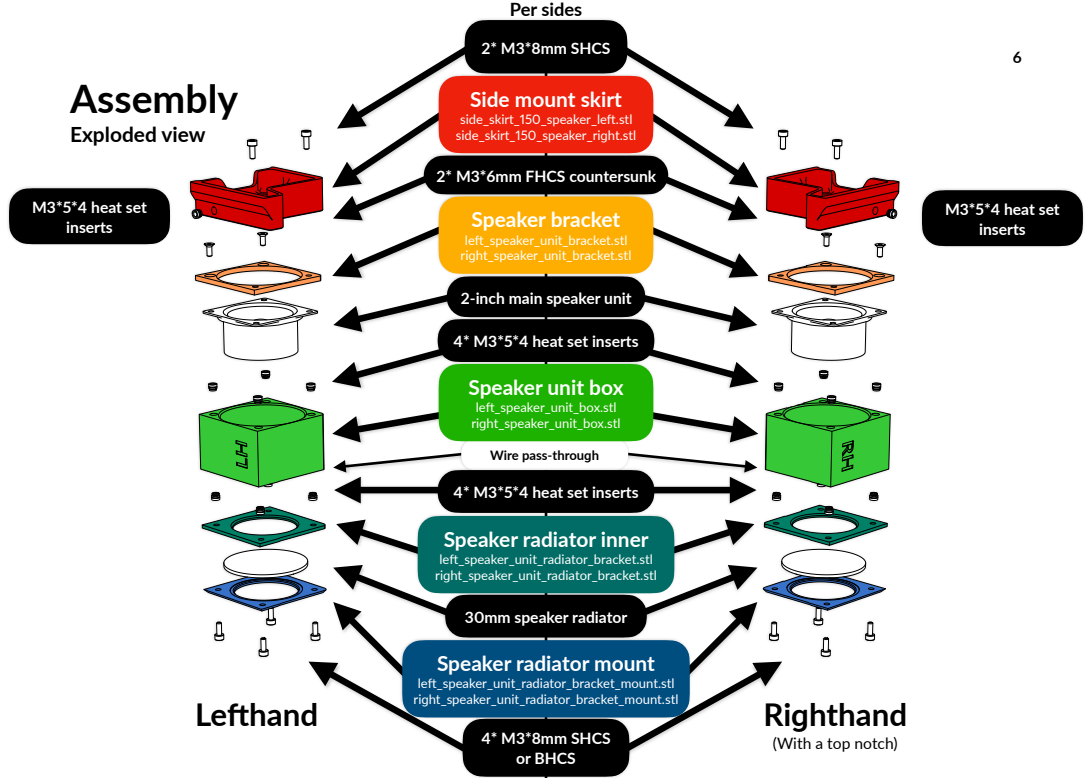
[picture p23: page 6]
Exploded view; Lefthand; Righthand; 2* M3*8mm SHCS; Speaker bracket; left_speaker_unit_bracket.stl right_speaker_unit_bracket.stl; 4* M3*8mm SHCS or BHCS; 2* M3*6mm FHCS countersunk; M3*5*4 heat set inserts; Per sides

Side mount skirt
side_skirt_150_speaker_left.stl
side_skirt_150_speaker_right.stl

2-inch main speaker unit

4* M3*5*4 heat set inserts
Speaker unit box
left_speaker_unit_box.stl
right_speaker_unit_box.stl

Wire pass-through
Speaker radiator inner
left_speaker_unit_radiator_bracket.stl
right_speaker_unit_radiator_bracket.stl

30mm speaker radiator
Speaker radiator mount
left_speaker_unit_radiator_bracket_mount.stl
right_speaker_unit_radiator_bracket_mount.stl

(With a top notch)

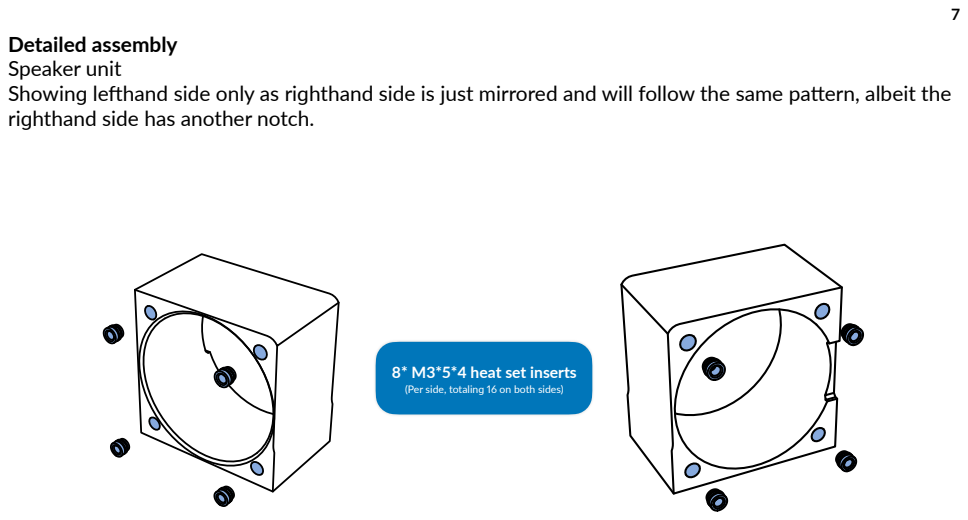
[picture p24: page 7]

Detailed assembly
Speaker unit
Showing lefthand side only as righthand side is just mirrored and will follow the same pattern, albeit the
righthand side has another notch.

8* M3*5*4 heat set inserts
(Per side, totaling 16 on both sides)

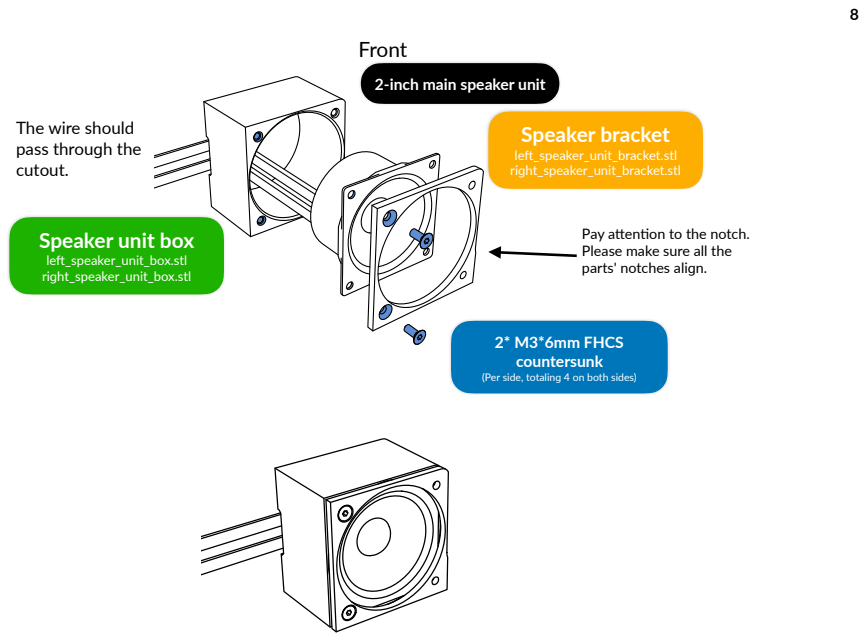
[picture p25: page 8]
Speaker bracket; left_speaker_unit_bracket.stl right_speaker_unit_bracket.stl; Front

2-inch main speaker unit

The wire should
pass through the
cutout.

Speaker unit box
left_speaker_unit_box.stl
right_speaker_unit_box.stl

Pay attention to the notch.
Please make sure all the
parts' notches align.

2* M3*6mm FHCS
countersunk
(Per side, totaling 4 on both sides)

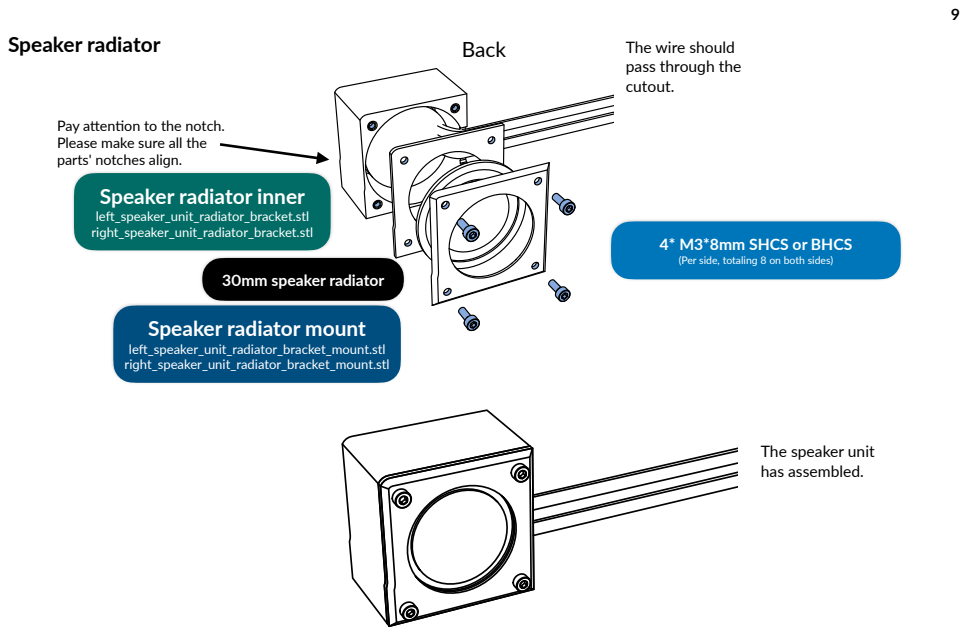
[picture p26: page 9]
Speaker radiator; Back

The wire should
pass through the
cutout.

Pay attention to the notch.
Please make sure all the
parts' notches align.
Speaker radiator inner
left_speaker_unit_radiator_bracket.stl
right_speaker_unit_radiator_bracket.stl

4* M3*8mm SHCS or BHCS
(Per side, totaling 8 on both sides)

30mm speaker radiator
Speaker radiator mount
left_speaker_unit_radiator_bracket_mount.stl
right_speaker_unit_radiator_bracket_mount.stl

The speaker unit
has assembled.

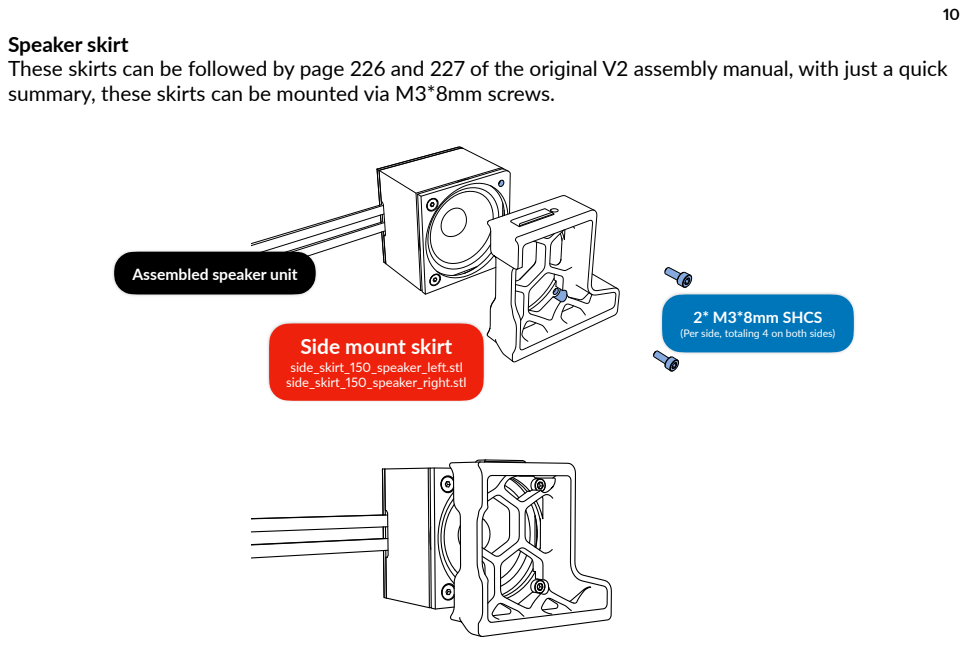
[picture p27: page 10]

Speaker skirt
These skirts can be followed by page 226 and 227 of the original V2 assembly manual, with just a quick
summary, these skirts can be mounted via M3*8mm screws.

Assembled speaker unit

2* M3*8mm SHCS
(Per side, totaling 4 on both sides)

Side mount skirt
side_skirt_150_speaker_left.stl
side_skirt_150_speaker_right.stl

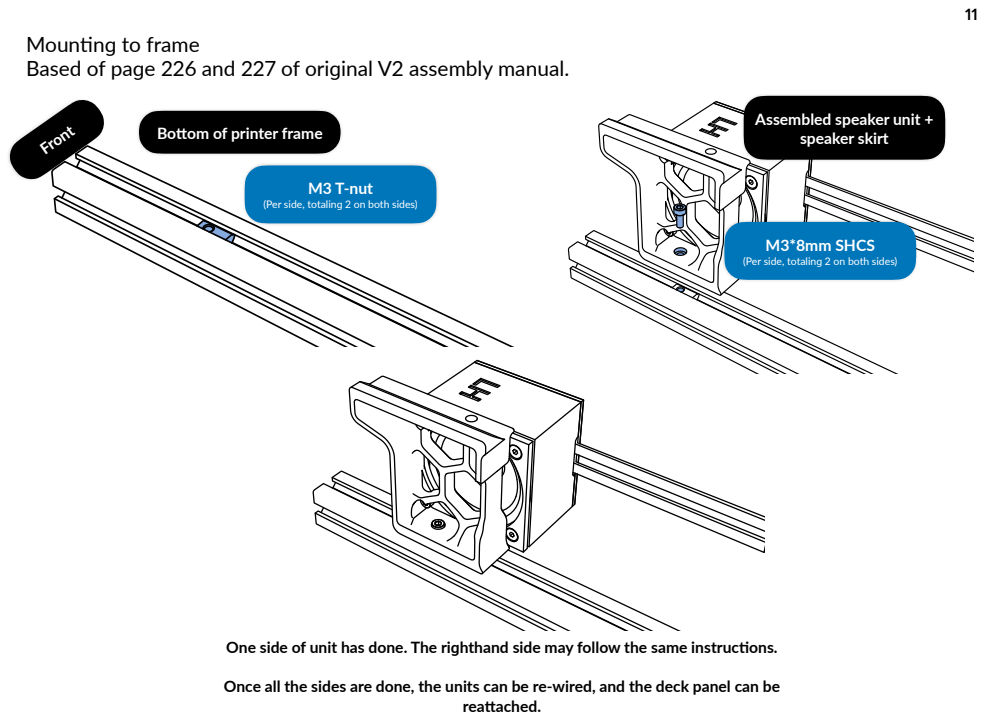
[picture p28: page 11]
M3 T-nut; reattached.

Mounting to frame
Based of page 226 and 227 of original V2 assembly manual.

Assembled speaker unit +
speaker skirt

Bottom of printer frame Front

(Per side, totaling 2 on both sides)

M3*8mm SHCS

One side of unit has done. The righthand side may follow the same instructions.

Once all the sides are done, the units can be re-wired, and the deck panel can be

12

# Software configuration

If the sound has too much treble, which might be, you may see showing the speakers bass potential. Debian / Ubuntu
There is a definite guide from MAGICPHOENIX. (https://mpx.wiki/Sound) If you want to tune ALSA- (alsa-lib) driven audio, you can use AlsaMixer. Note: the speakers are 10x louder, so it's best to tune down the volume to just 6 to 25%. You can install libasound2-plugin-equal, and then define it, but this is too difficult and not production-ready.
- You can open AlsaMixer by typing alsamixer at the terminal of the machine.
- In case there are multiple speakers or sound cards, to change the current sound card, press F6 to show the sound card selection menu.
- To adjust the volume, press F5, then use up or down arrow keys to adjust the volume. Since banger speakers are very intrusive, it is generally recommended to set the volume to just 6 to 25%, otherwise there will be a fatal mistake where something yelling emitted.
- You must manually save the changes by typing sudo alsactl store . This requires superuser privilege. Not typing such command will lose changes, and you know what will happen above.
- You can install plugins or even force ALSA to use your preferred speaker / sound card on start-up by creating asound.cfg under /etc/. (https://mpx.wiki/Sound#creating-asoundconfig)
If you are using Debian / Ubuntu with desktop environment, you can use EasyEffects to tune and equalize the speakers.
Klipper
Klipper does not have sound playing on its own, but users are able to use Klipper software to allow their machines play audio. There are two ways to make it happen, but the second method is less vulnerable to hacking. If Klipper is in Debian virtual machine, you may also see "What if Debian is in virtual machine?".

13
Uploading audio files to machine
- To place audio files into your machine, the best way to do is to drop & upload the file through lightweight interface (Mainsail / fluidd). First, create a folder called audio just to make sure it is organized, and then drop the audio file you like it to play to such folder.
Klipper Gcode Shell
This method is more popular. There is a video by Stacking Layers (https://youtu.be/mExUlFUlSpw) and a (previously mentioned) guide from MAGICPHOENIX. Basically, you upload the audio file to the organized directory and then set up the Gcode shell command that allows playing audio via aplay and set up the command that executes such shell command.
- Shell command to play sound: aplay /home/pi/printer_data/config/audio/sound.wav # if username is pi, using the modern Klipper file structure and the sound file is WAV placed in audio subfolder. Direct implementation
This method is less vulnerable to hacking, if it does not use superuser privilege. There is an article written by Al Williams on Hackaday (https://hackaday.com/2024/10/08/3d-printering-listen-to-klipper/) that puts such implementation to the Klippy extra folder, and users can assign an aplay entry and aplay Klipper command to play the audio.

Windows
If the enhancements options such as bass are available, you can optionally tune the speakers. To find speaker software enhancements in Windows 11, go to settings, and then system, then sound. After that select more sound settings, which will pop up sounds window. Select the speaker that powers this and find enhancements.

14
What if Debian is in virtual machine?
If you want sounds played by Klipper or aplay in Debian VM, you need to enable the audio for the virtual machine (you may need to shut it down first), if obviously disabled. On VirtualBox, go to settings of Debian VM with Klipper, then select audio, and then check enable audio, after that, check enable audio output under extended features section. You may keep the other settings unchanged.

Showing the speakers bass potential
Under Oitswilliam's intensive research, by that I mean 5 minutes, the speakers will show the bass potential (and sound good) on 150Hz at 6dB bass boosted equalizer. You may tune it around such range, around 80 to 200Hz, 3 to 6dB. If the speakers sound good without any tuning, then this is not required. Note that Oitswilliam is not an audiophile expert, please ask the professionals on choosing better hardware around.

Troubleshooting
The speakers are not playing, or is playing through other instruments!
Some software decided to use another instrument instead of the driver that powers banger speakers. You can force using the banger speakers by manually setting.
- On Windows, go to settings, and then system, then select sound. You will see the speakers connected. Select the speaker that power the banger speakers.
- On Debian with GNOME desktop environment / Ubuntu, the procedure is similar, go to settings, then sound. You will see the speakers connected.
- On Debian WITHOUT the desktop environment, you must use ALSA (alsa-lib) CLI. Please check Debian / Linux section for the exact procedure.

15

# Assembly complete

And we are done! If you are satisfied with such product consider tagging @officialbunny350 on Facebook, @oitswilliam on Instagram or @realBunny350 on X (formerly known as Twitter) and share such product with us on Oitswilliam Pang Discord Server.

If you have enquires, problems or issues related to building or using such product, please report it on GitHub.com/Bunny350/OitswilliamV2/issues and we will get on it.

Change log
- 2026-06-16 - Minor adjustment, change Oitswilliam's Instagram handle.
- 2026-06-15 - Update OitswilliamV2 logo and capitalization.
- 2026-03-18 - Add software configuration section about implementing sound output to Klipper and speaker tuning through basic software. Add Instagram link as Oitswilliam came back there.
- 2026-01-24 - Minor adjustments, re-sort the beginning of the manual, minor adjustment to last steps in page 11. Re-use the current logo on the front page.
- 2026-01-08 - initial release

Manual designed by Oitswilliam Pang. One-person operated design. www.oitswilliam.com

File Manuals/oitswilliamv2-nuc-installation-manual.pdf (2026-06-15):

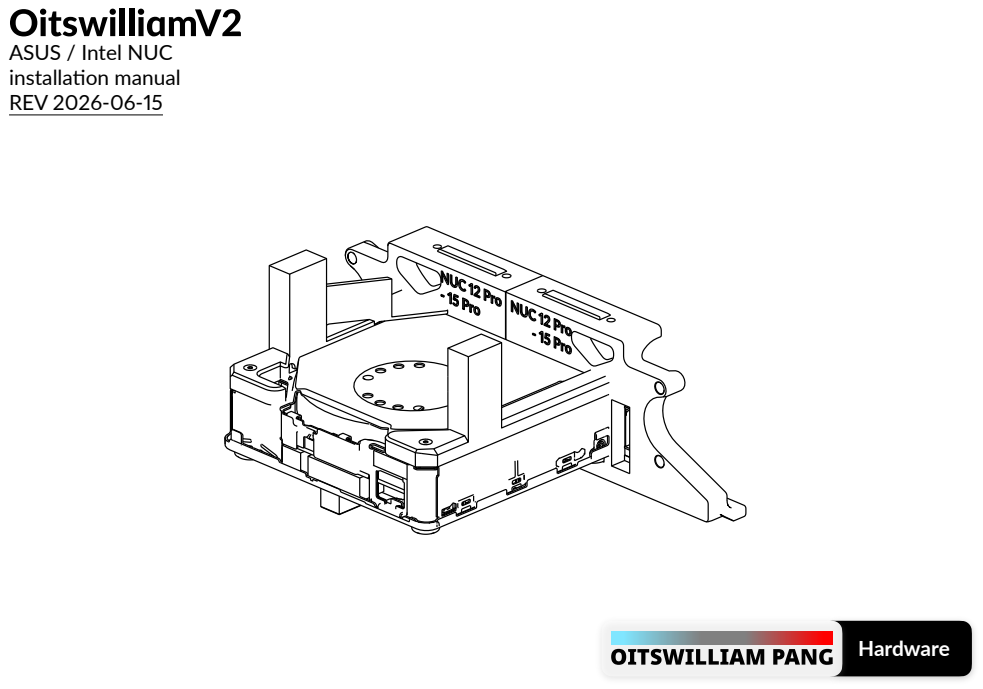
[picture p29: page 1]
Hardware

ASUS / Intel NUC
installation manual
REV 2026-06-15

2

# Contents

- Before getting started
- Recommended Intel mobile CPUs (and AMD Ryzen mobile CPUs) for tasks
- About OitswilliamV2 NUC mount
- Assembly
- Modify NUC
- Skirt preparation
- Install the module (ASUS / Intel NUC)
- Hardware connection guide
- Software configuration
- Debian Linux physical
- Windows 11 physical + Debian Linux VM

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
# Before getting started

You are about to read OitswilliamV2 NUC installation manual.

This mod attaches ASUS / Intel NUC computer into the printer in absolute back side of the Voron printer. Currently it only supports V2.4 150mm mod spec and have no intents of extending the support to other Voron printers.

Guide and legend

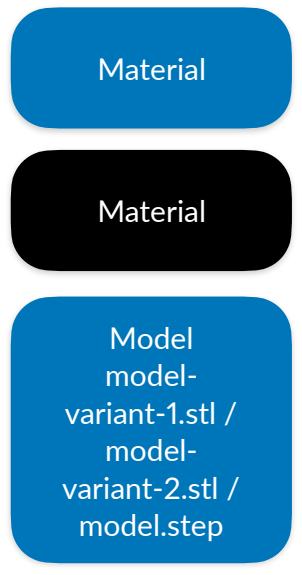
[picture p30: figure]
Material; Model model- variant-1.stl / model- variant-2.stl / model.step

- highlighted material / part
- mentioned material / part
- printable / moldable model (these includes STL, 3MF or sometimes even source files
like STEP)
The model name may not be mentioned in later pages.

Electronic parts will show their own power throughout this
assembly guide, but here are the abbreviations that will be used:
V - volt,
A or I - amp (I as amp may be used but not in this manual.),
GND - ground.
In DC,
+ - positive,
- - negative
In AC,
L - live
N - neutral
⏚, E or G - earth ground
Other abbreviations include: MCU - microcontroller unit SBC - single-board computer

4
Warning
Danger: unless if it only runs on DC and only has a DC input, otherwise risk of electric shock
- Even though you can build with this mod from start, if you want to wire, or re-wire, you need to make sure and check that the mains is unplugged.
- Failure doing so which is unplugging the mains power may cause electrocution or even death.
- When in doubt, please don't touch the wires connected to the power supply or SSR.
Caution: static electricity. It is recommended to wear with at least the compliant wrist strap (may be it with 1-megaohm resistor from contact to earth) that is properly connected to earth.
Part printing
The parts of this model can be printed in the base color of the printer. Bold text indicates the recommended value and italic text indicates on what setting / value it needs to set.

Additional maker tools
To get started building the project, you may use the following tools:
- Wire crimping tool
- Soldering iron
- Heat shrink tubings, in 5mm diameter, one color minimum, two colors recommended.
FDM / FFF or SLS | Print material: ABS, ASA or PA12, prohibits PLA.
Layer height of 0.2mm, initial layer height can be 0.2mm or higher. | Nozzle and extrusion width must be forced 0.4mm; if using 0.4mm nozzle
1.6mm wall width, or 4 wall counts. | Infill must be at least 40%, except on the infill modifiers.
At least 4 solid bottom and top layers, except on the infill modifiers. | The best print speed is up to 120mm/s. The speed might be reduced by the hot end flow rate.
Supports are recommended for main skirt parts. Use tree or organic supports if available. | Other settings might be depended on your printer. Follow it's warnings for proper handling.

5
Recommended Intel mobile CPUs (and AMD Ryzen mobile CPUs) for tasks

To those who will be saying "I should get one with Celeron CPU," the problem is that Celeron often is trash, well only if we give Windows native to it. Beside this, Core 3 might have the same issue as Celeron's so it is not recommended to run Windows natively and Klipper virtualized.
CPU IDs: Celeron (4c): N5105, Core 3 (2p4e): 100U (this doesn't have low-power efficiency cores, let alone ray-tracing enabled GPU), Core Ultra 5: 125H (4p8e2l), Core Ultra 7: 155H (6p8e2l). Core identifiers p=performance core, e=efficiency cores, l=low-power efficiency cores, c=generic cores.
Task | Celeron (4c) | Core 3 (2p4e) | Core Ultra 5 / Ryzen 5 | Core Ultra 7 / Ryzen 7
Run Linux with desktop environment | Suitable | Suitable | Suitable | Suitable
Can I run Windows natively and Klipper virtualized? | No | No | Probably, but we don't want planned obsolescence to ever exist, so no | Yes
Stronger than average computers, such as schools'? | No | No | Yes | Yes

6
Recommended parts
This mount is intended to install NUC 14 Pro (slim version) or 15 Pro (slim version), although older versions that is using 12th gen Intel Core or later still work. Other versions or variants may not fit properly, like need reverting for Pro tall version / Pro Plus, or just incompatible with Pro AI or ROG NUC.

Note that this selection is very picky, if there is a variant selection for NUC Pro, choose the slim version.

Compatible | Incompatible
NUC 12 Pro, 13 Pro, 14 Pro, 15 Pro, slim version (models with K) | NUC 12 Pro, 13 Pro, 14 Pro, 15 Pro or so on, tall version (models with H)
| NUC 14 Pro Plus, 15 Pro Plus and so on
| NUC 14 Pro AI
| NUC Essential, doesn't matter whether it's Intel or ASUS
| NUC Performance (ASUS), ROG NUC and NUC Enthusiast (pre-ASUS)
| NUC Pro X / NUC Extreme
| NUC 11 Pro or earlier generations (normally, please request to us or create from blank.)

7
Incompatible NUC models
- NUC 11 Pro
- Did not have second method of powering. See connectors used.
- This has already required modifications for the skirt.
- NUC 12 Pro, 13 Pro, 14 Pro, 15 Pro, tall version (models with H)
- Device too tall, needs reverting to slim version
- NUC 14 Pro Plus and 15 Pro Plus
- Form factor too big, needs reverting to Pro slim version
- NUC 14 Pro AI
- Device seems only be intended for personal computing on the desk.
- Different form factor.
- Loses front panel connection.
- Device doesn't seem to be intended for embedded solutions.
- NUC Essential, doesn't matter whether it's Intel or ASUS
- Different form factor.
- For NUC 14 Essential or later, it loses front panel connection.
- NUC Performance (ASUS), ROG NUC and NUC Enthusiast (pre-ASUS)
- Different form factor and too big.
- NUC Pro X / NUC Extreme
- Device seems only be intended for personal computing on the desk.
- Different form factor, the computer assembly is card-based. The compute unit is too.
- Device doesn't seem to be intended for embedded solutions.

8
- For NUC Performance (Intel), since they have different port arrangement and we weren't intended to make that, so we have to put the lineup incompatible. And for NUC 11 Pro, it only powers via barrel jack, but we normally do not support it, so we have to put that lineup incompatible as well. If you need it, you can request for such compatibility or modify the blank mounting panel.
- NUC Performance was the old name for NUC Pro, before the one with 11th generation Intel Core.
- For NUC 16 Pro, the form factor is different, and is on the works. The form factor requires changing the Z axes motors with Clockwork (first generation) motors first.
- For other (non-ASUS or Intel) "NUC"s, since they did not provide CAD references, we did not make for these.
- For requirements:
- Height limit of 36mm, excluding feet, or total of 40mm,
- Width and depth limit of 130mm, if slotting to the skirt, or 150mm if changing motors be the requirement.
- Must support "backpack" via VESA monitor mount.
- Unless if the NUC can't slot into the skirt, the NUC must slot in 8.4 to 8.2mm to the skirt (or the IO shield must have at least 1.2 to 1.4mm of thickness).
- If the NUC is not enclosed in exoskeleton (dual-casing design), it may be difficult to be placed into the skirt, and may rely on legacy back skirt.

Connectors used
- DC2 (Molex Micro-Fit 3.0 2*2P connector)
- Used to power the NUC if not using with the included barrel jack power supply.
- Front panel power button (DuPont 2.0mm pitch, 2-pin recommended, connector that utilize all pins will render the bottom cover unusable)
- Used to power the NUC on via RealEstate display.

9
Other information
- You may read the service manual for your NUC through ASUS Support or the vendor that make such mini PC. This manual may not serve some information or material where the service manual has written.
- RealEstate G2.1 from OitswilliamV2 mod is recommended prior installation. This unit comes with the power button that can be connected to the PC / SBC.

About OitswilliamV2 NUC mount
The NUC mount is one of the key parts of OitswilliamV2. This is one of the stupidly insane task as no one has thoughts about, yet magical, it grants printers performances no budget laptops can achieve. It uses ASUS NUC Pro as it's base and mounts the computer to the back of the skirt. It will power the future of user experience.
This mod is (vaguely) inspired by NucDeck by CNCDan, (https://github.com/dmcke5/NucDeck) except that the NUC is shoved into the printer instead of the game console controller.
Contribution
This mod is a part of OitswilliamV2 mod project through GitHub. You can visit, contribute and report new issues here. (https://github.com/Bunny350/OITSWILLIAMV2/)
Technical support
You can contact Oitswilliam here. (http://oitswilliam.com/support) You can email or direct message Oitswilliam in Facebook. Or if the issue is not related to OitswilliamV2 mod, but rather most of Voron parts, you may visit Voron forum or its Discord server.

# Assembly

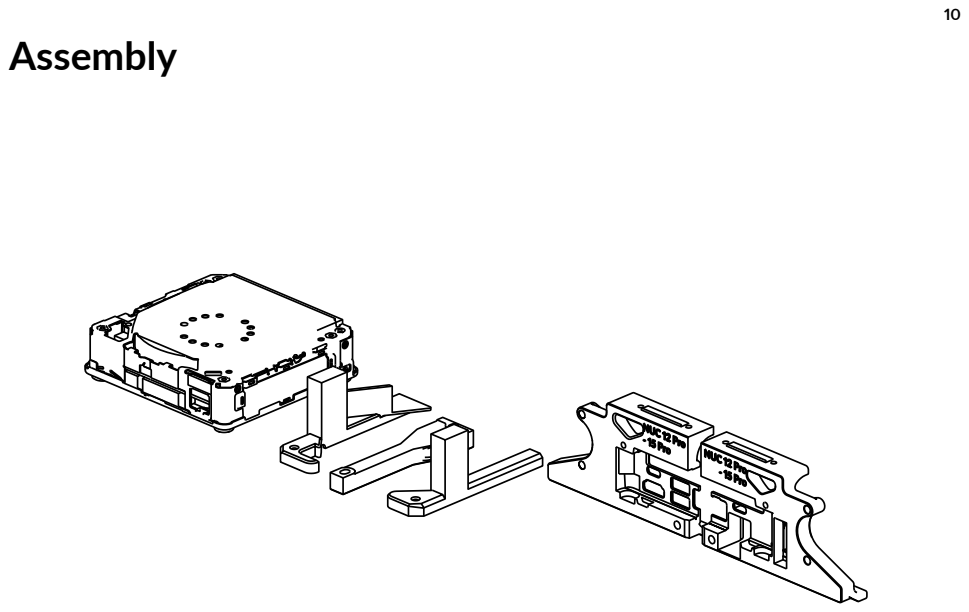
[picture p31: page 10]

11
Modify NUC
The NUC needs to be modified before being attached to the skirt and be put on the printer. If you do not do this procedure and just put it on the printer, then it is too late and needs disassembly.
Make NUC top-naked
The design of the NUC mount requires the PC to be top-naked, to improve its cooling when housed inside the printer.

### 1. Unclip the top cover

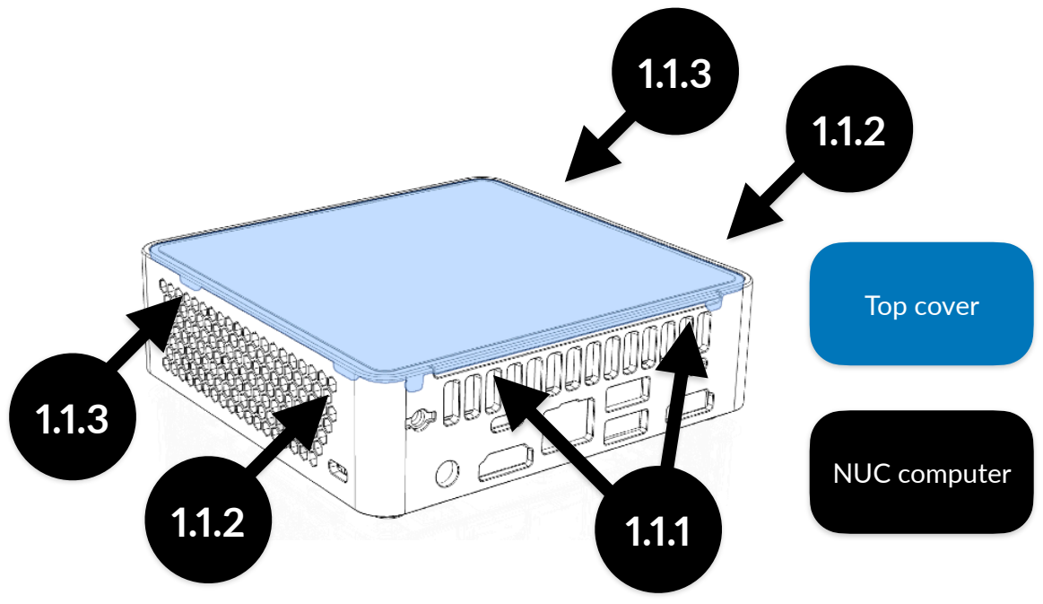
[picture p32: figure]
NUC computer; Top cover

To unclip the top cover, start prying at left- and right-back side between the top cover and the plastic case (1.1.1), then go from back (1.1.2) to front (1.1.3). When unclipped correctly, the top cover can be removed.

12

### 2. Disconnect the antenna cable (ASUS NUC 14 Pro and NUC 15 Pro)

If you are using NUC 14 Pro or NUC 15 Pro, you need to disconnect the antenna with the black cable (or as technicians call it main antenna), otherwise you will break the cable removing the plastic case. For Intel / ASUS NUC 13 Pro or earlier, this is not required.

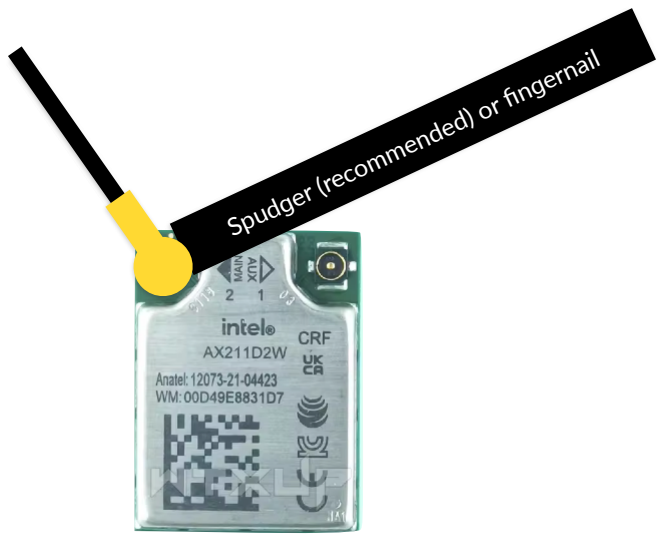
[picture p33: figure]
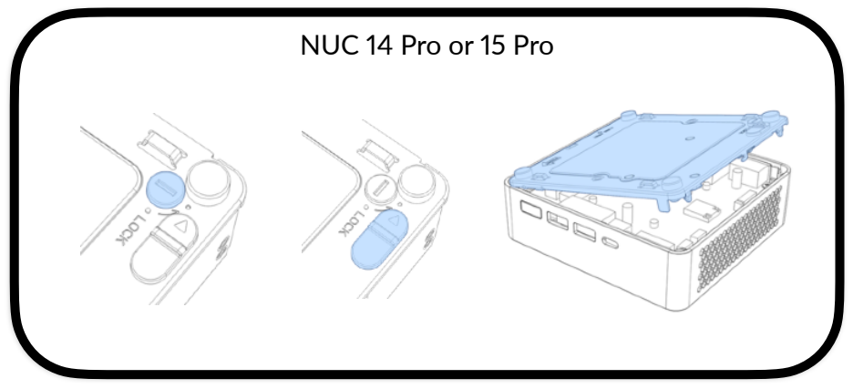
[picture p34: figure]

This step is not required if you have ASUS / Intel NUC 13 Pro or earlier, or ASUS NUC 16 Pro.
Open the bottom cover, unlock and push the latch, then disconnect the black cable from the Wi-Fi + Bluetooth transceiver with the Spudger (recommended) or finger nail.
NUC 14 Pro or 15 Pro | Spudger (recommended) or fingernail

13
After that, get the black antenna cable out of the shell. Carefully pull the cable up from the plastic housing.

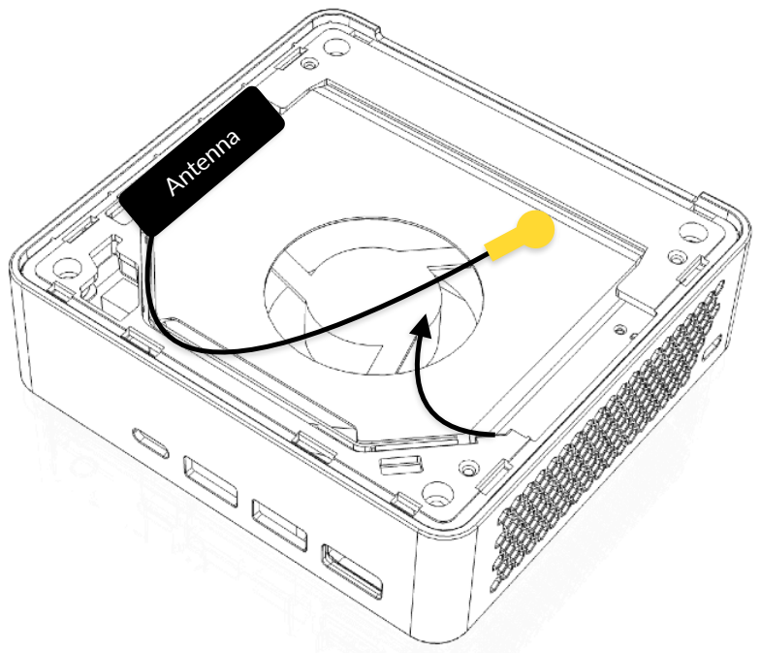
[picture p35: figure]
Antenna

14

### 3. Remove the plastic housing

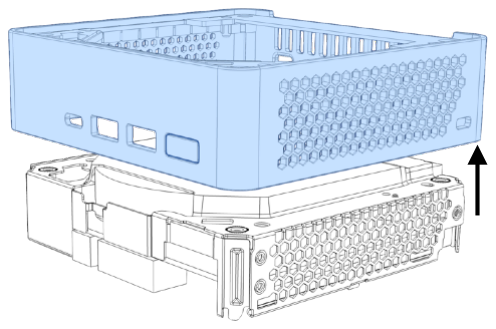
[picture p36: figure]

Start by removing four M2.5*5mm Phillips P1 screws, then pitch and unclip the front side first (3.2.1), and then unclip the back side (3.2.2).

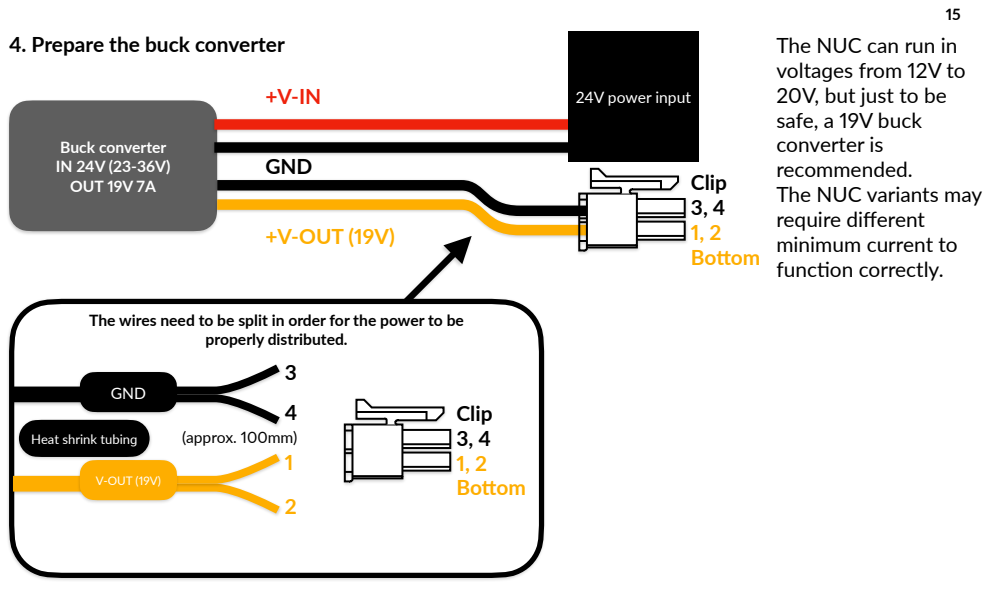
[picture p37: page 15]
4. Prepare the buck converter; The NUC can run in; GND; +V-OUT (19V); Buck converter IN 24V (23-36V) OUT 19V 7A; 24V power input; Clip 3, 4 1, 2 Bottom; properly distributed.; V-OUT (19V); Heat shrink tubing; (approx. 100mm)

voltages from 12V to
20V, but just to be
safe, a 19V buck
converter is
recommended.
The NUC variants may
require different
minimum current to
function correctly.

The wires need to be split in order for the power to be

16

### 5. Remove the bottom cover, if re-attached prior

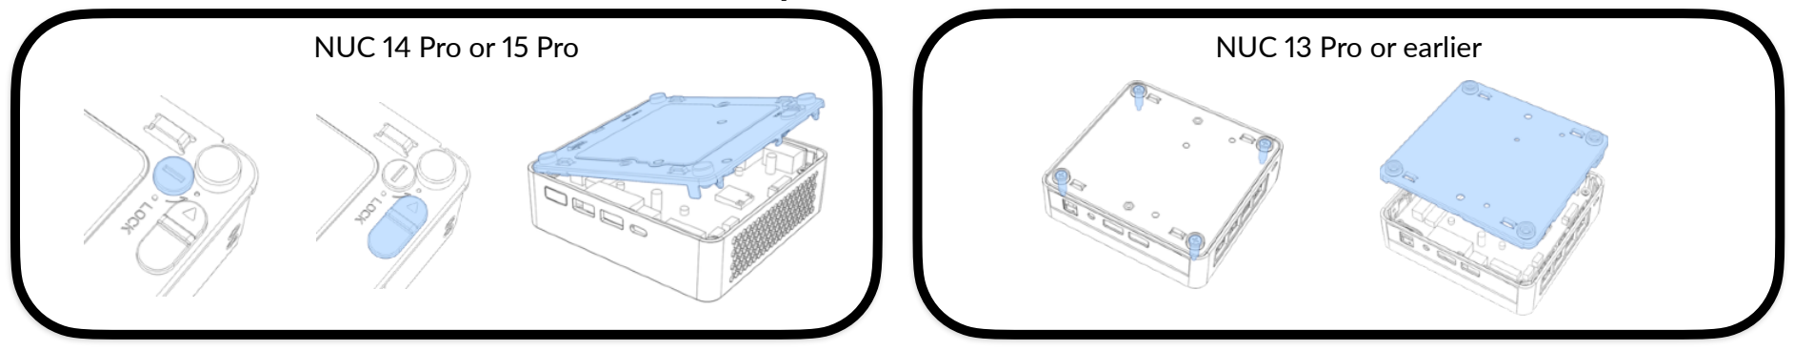
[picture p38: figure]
NUC 13 Pro or earlier; NUC 14 Pro or 15 Pro

### 6. Disconnect the antenna cable, main (NUC 12 and 13 Pro) and auxiliary cable(s)

For NUC 14 Pro and 15 Pro, unless if the cover was stayed removed, push the latch and then turn the bottom to remove it.
For NUC 13 Pro or earlier, unscrew four 1315 (M2.5*18 captive) screws in legs, then pull the whole bottom cover to remove it.

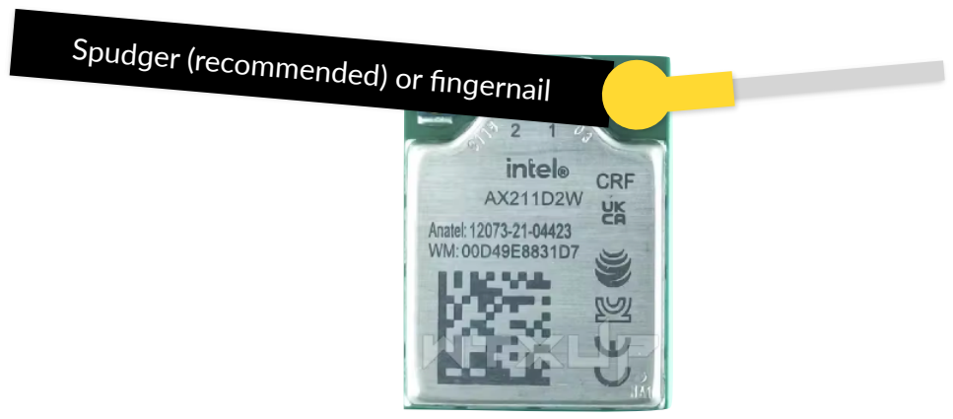
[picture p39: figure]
Spudger (recommended) or fingernail

Disconnect the white cable from the Wi-Fi + Bluetooth transceiver using the Spudger (recommended) or finger nail. If the black cable is not disconnected yet, it should be disconnected as well. This is to prevent damage.

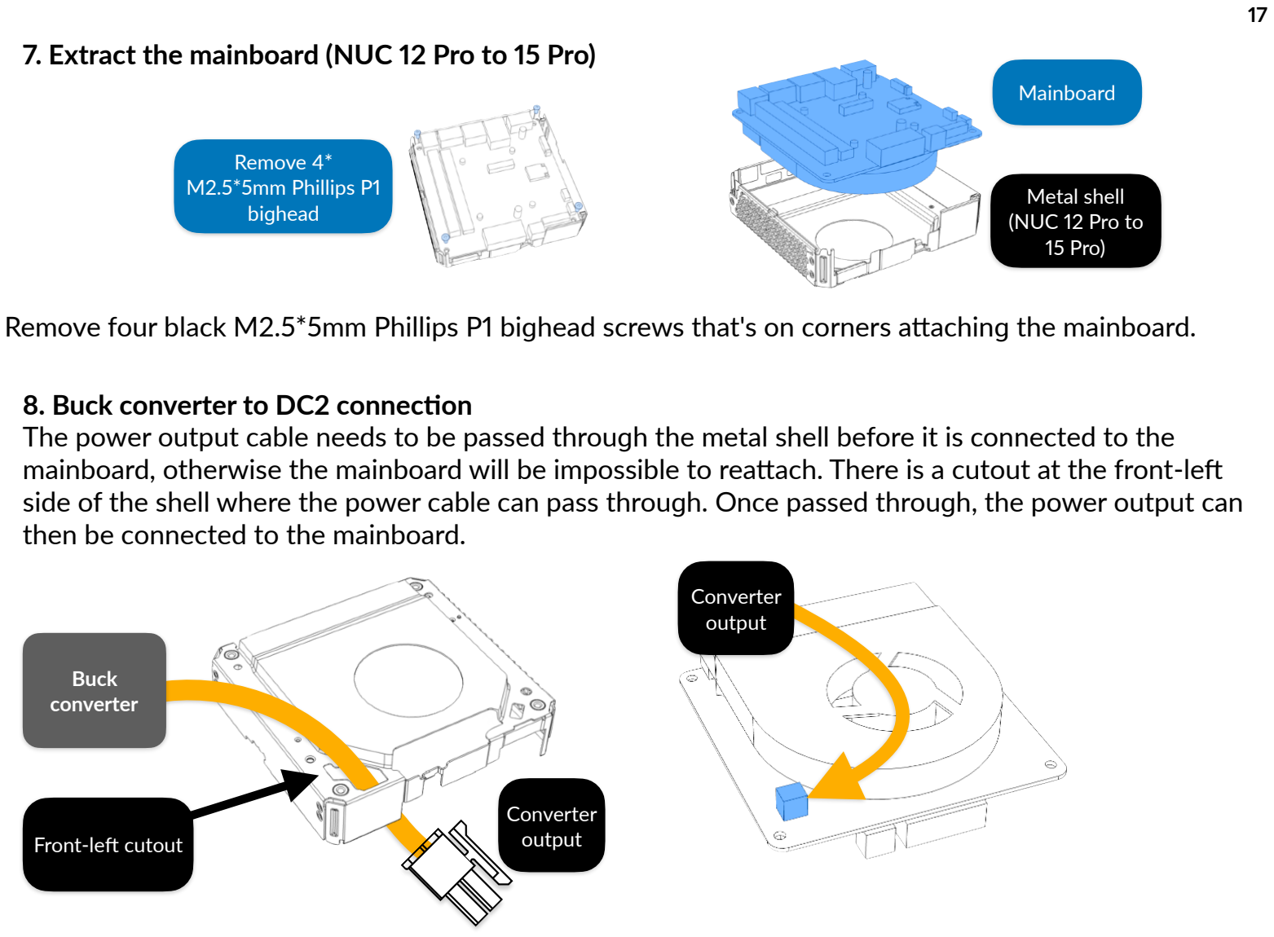
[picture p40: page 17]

17

### 7. Extract the mainboard (NUC 12 Pro to 15 Pro)

### 8. Buck converter to DC2 connection

The power output cable needs to be passed through the metal shell before it is connected to the mainboard, otherwise the mainboard will be impossible to reattach. There is a cutout at the front-left side of the shell where the power cable can pass through. Once passed through, the power output can then be connected to the mainboard.

Remove four black M2.5*5mm Phillips P1 bighead screws that's on corners attaching the mainboard.

Remove 4*
M2.5*5mm Phillips P1
bighead

Mainboard

Metal shell
(NUC 12 Pro to
15 Pro)

Converter
output

Buck
converter

Front-left cutout

Converter
output

18

### 9. Reassembly, without the plastic housing, but with front panel power button extension

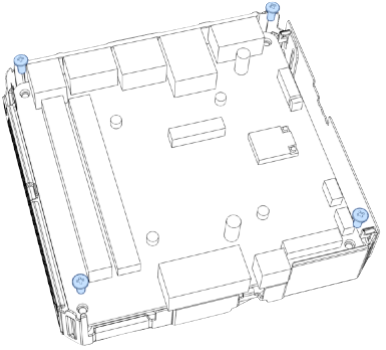
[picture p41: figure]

You may do the reverse of what you have opened, but without the front plastic housing. First, carefully reattach the mainboard (as the converter output is connected), and secure it with four black M2.5*5mm Phillips bighead screws,

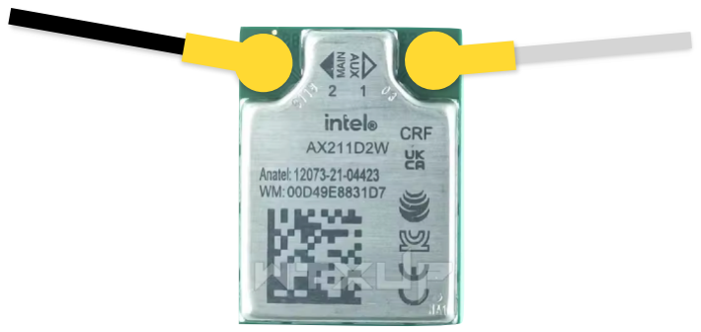
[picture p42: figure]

Then, re-connect the antenna cables, Spudger may help, make sure the cable colors and the arrows match.

Mainboard

Metal shell
(NUC 12 Pro to
15 Pro)

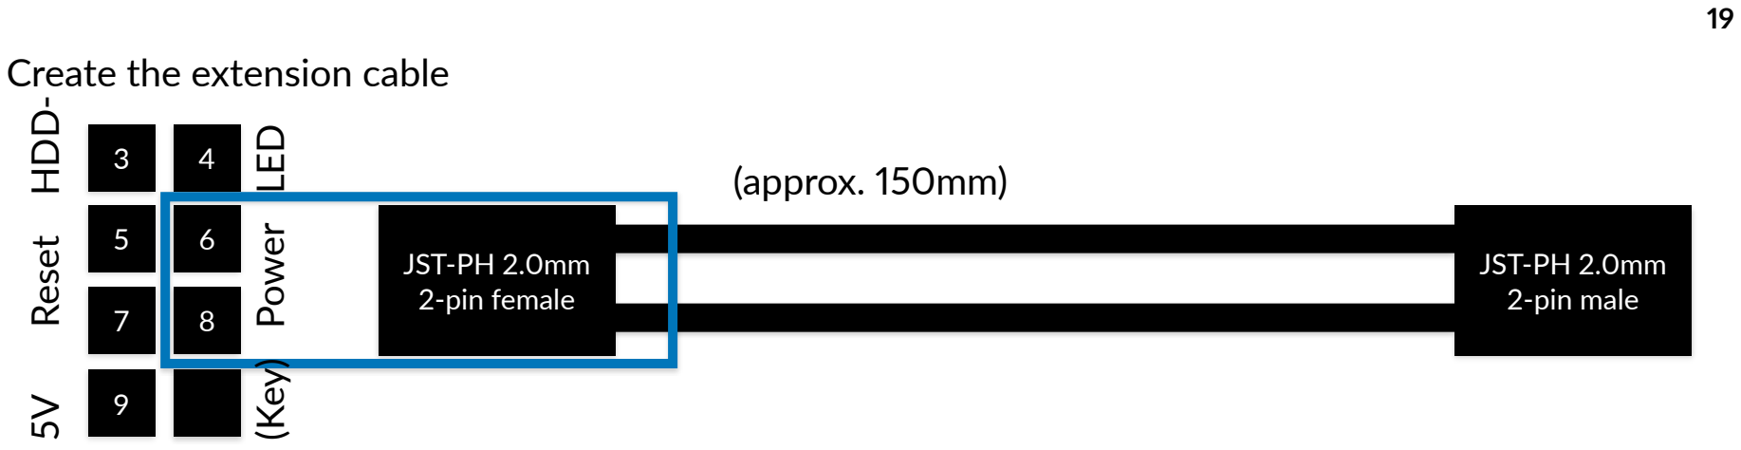
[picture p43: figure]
Create the extension cable; JST-PH 2.0mm 2-pin female; JST-PH 2.0mm 2-pin male; 5V Reset HDD-; (Key) Power LED; (approx. 150mm)

The polarity doesn't matter as we are just connecting to the button. You may connect the extension cable to the pins 6 and 8 of the front panel header. The first pin will have an arrow pointing at, and the tenth will not have a metal pin. The cable can be sled through between USB-C port and a USB-A port.

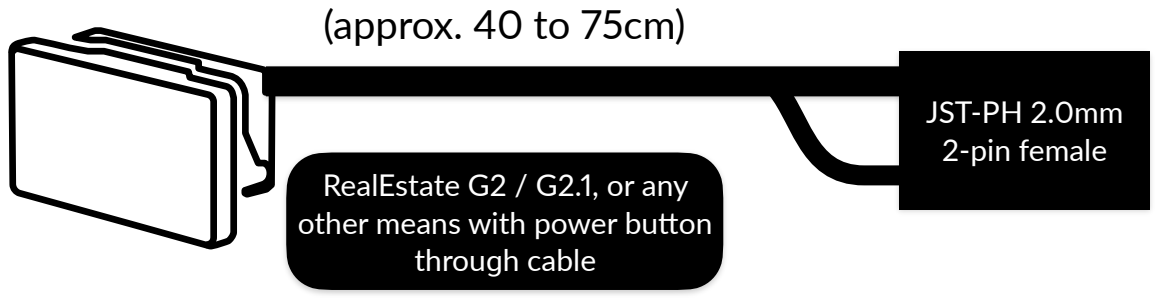
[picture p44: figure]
RealEstate G2 / G2.1, or any other means with power button through cable; JST-PH 2.0mm 2-pin female; (approx. 40 to 75cm)
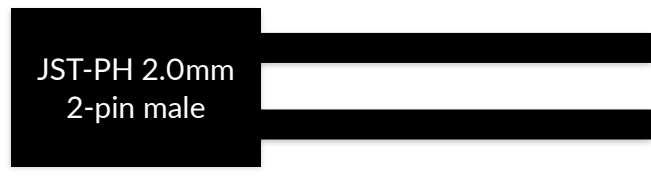
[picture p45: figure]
JST-PH 2.0mm 2-pin male

You may connect the power button cable to the front IO header extended by the extension cable after mounting NUC to the frame.
- And then, the M.2 PCIe NVMe SSD and DDR4 (NUC 12 Pro and 13 Pro) / DDR5 (NUC 14 Pro or later) RAM sticks can be loaded, if not loaded prior.

From the extended cable

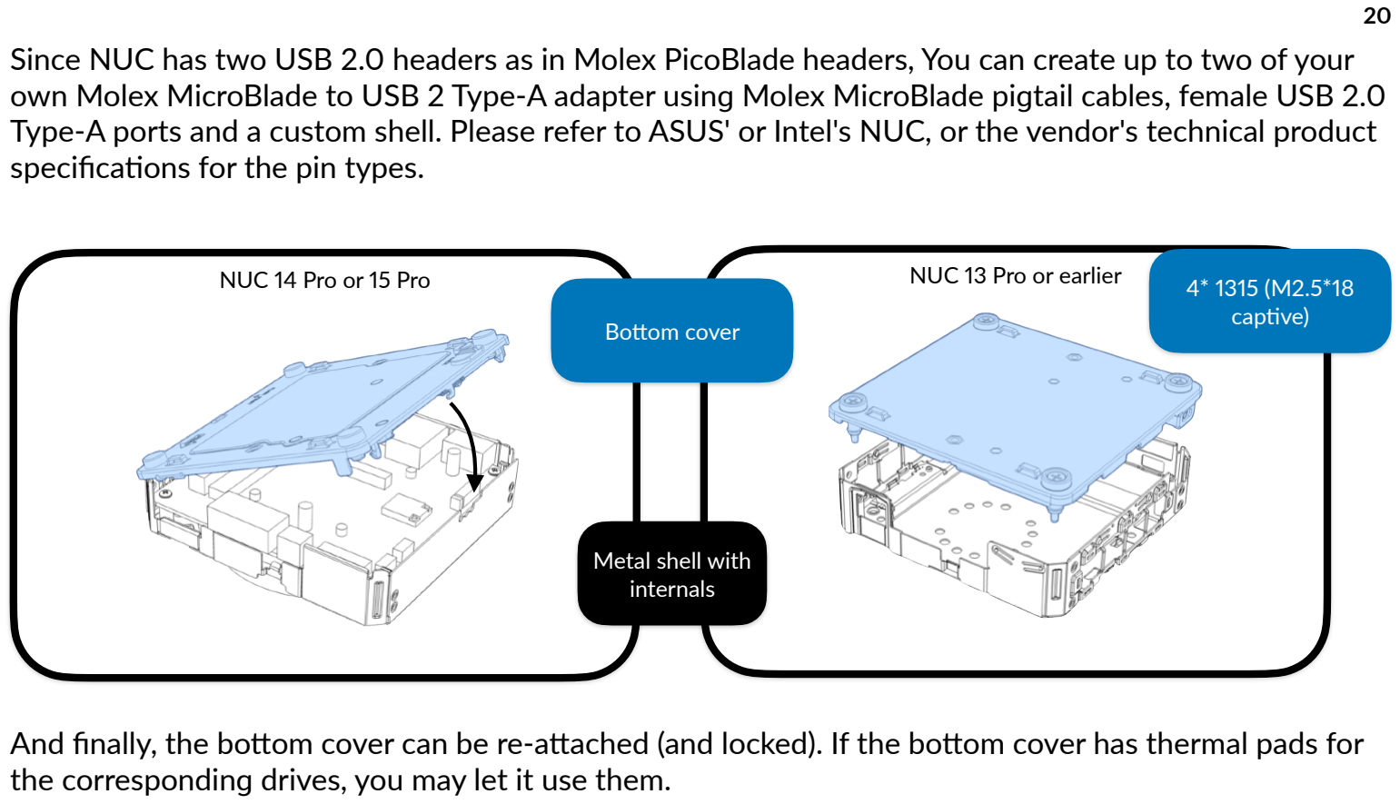
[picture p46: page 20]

20
Since NUC has two USB 2.0 headers as in Molex PicoBlade headers, You can create up to two of your own Molex MicroBlade to USB 2 Type-A adapter using Molex MicroBlade pigtail cables, female USB 2.0 Type-A ports and a custom shell. Please refer to ASUS' or Intel's NUC, or the vendor's technical product specifications for the pin types.

And finally, the bottom cover can be re-attached (and locked). If the bottom cover has thermal pads for the corresponding drives, you may let it use them.

NUC 14 Pro or 15 Pro | NUC 13 Pro or earlier

Bottom cover

Metal shell with
internals

4* 1315 (M2.5*18
captive)

21
Skirt preparation
There are additional heat-set inserts that will be placed at the bottom back face of the skirts, not just the front face and the bottom from the page 212 of Voron 2 assembly manual.

The top reinforcement studs also need heat-set inserts as well.

2* M3*5*4
heat-set inserts
(1 per side)

Righthand back skirt with NUC mount
back_skirt_nuc_pro_right.stl

Lefthand back skirt with NUC mount
back_skirt_nuc_pro_right.stl

2* M3*5*4
heat-set inserts
(1 per side)

Top left reinforcement stud reinforcement_stud_top_left_nuc1 2to15pro.stl

Top right reinforcement stud reinforcement_stud_top_right_nuc12to 15pro.stl

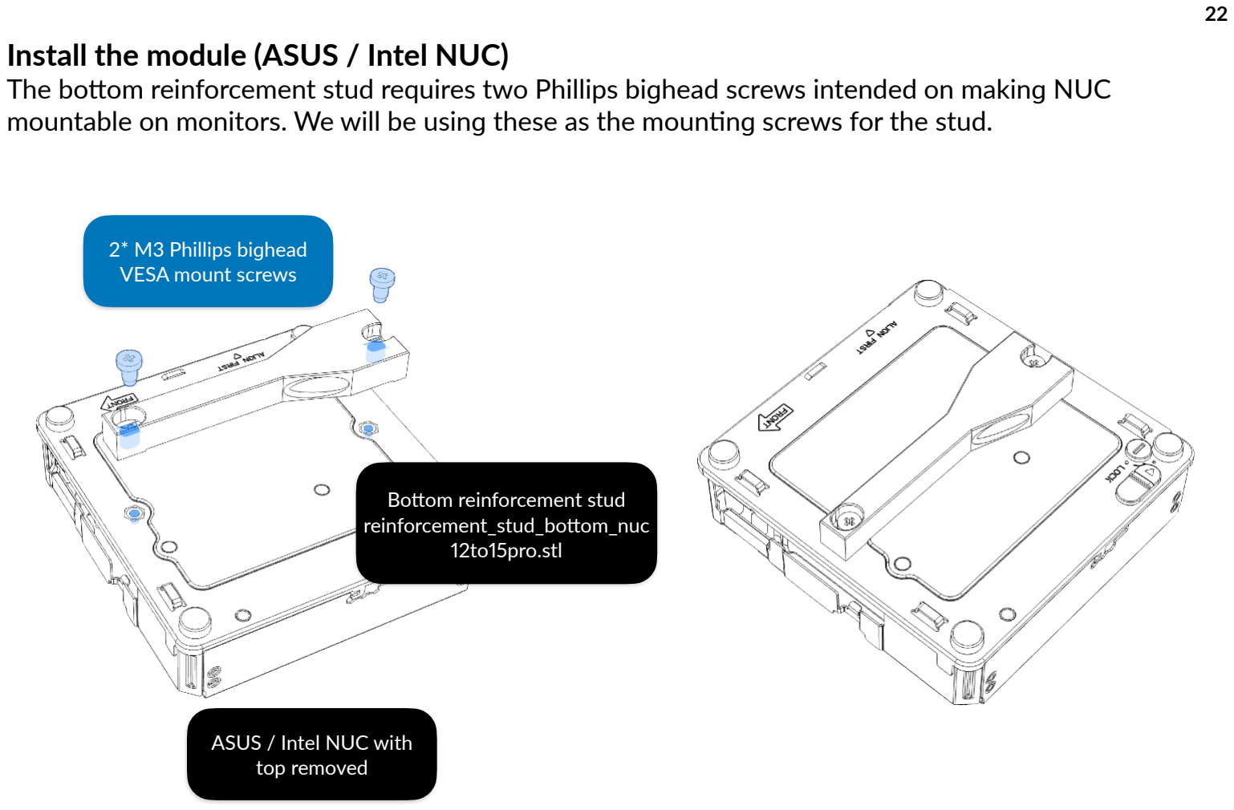
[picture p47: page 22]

22
Install the module (ASUS / Intel NUC)
The bottom reinforcement stud requires two Phillips bighead screws intended on making NUC mountable on monitors. We will be using these as the mounting screws for the stud.

2* M3 Phillips bighead
VESA mount screws

Bottom reinforcement stud
reinforcement_stud_bottom_nuc 12to15pro.stl

ASUS / Intel NUC with
top removed

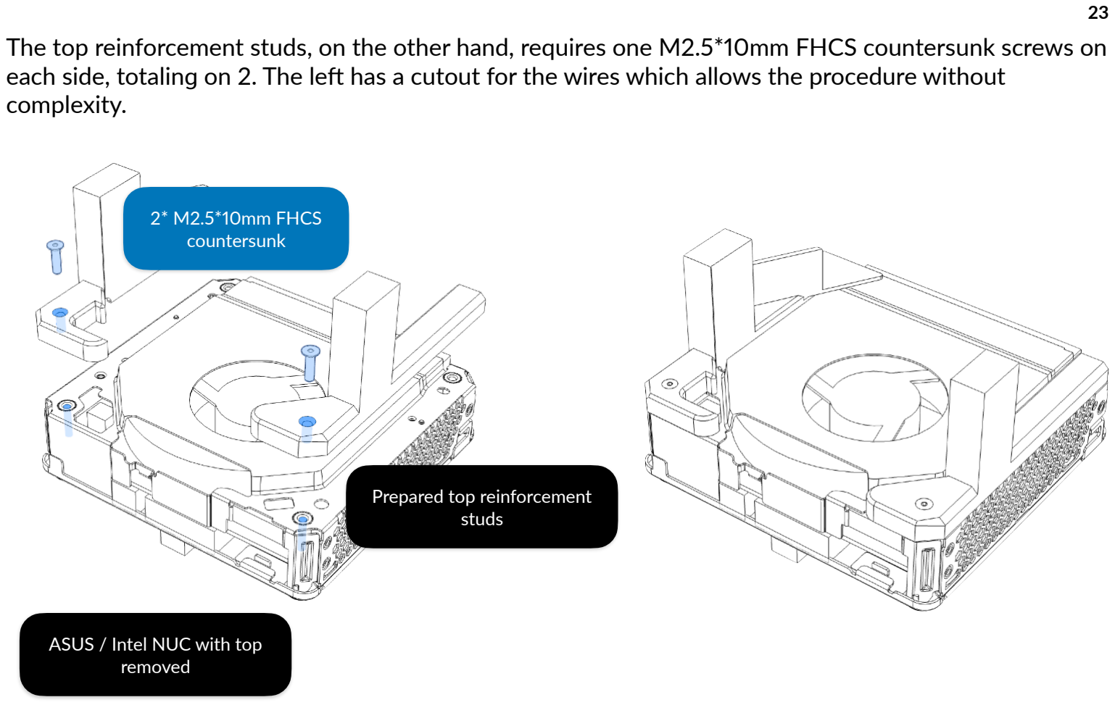
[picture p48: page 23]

23
The top reinforcement studs, on the other hand, requires one M2.5*10mm FHCS countersunk screws on each side, totaling on 2. The left has a cutout for the wires which allows the procedure without complexity.

2* M2.5*10mm FHCS
countersunk

Prepared top reinforcement studs

ASUS / Intel NUC with top
removed

24
The HDMI to flex cable and the FPC cable needs to be connected to the left side of the HDMI port before it is being inserted to the skirt.

If the skirt is being attached for the first time, the NUC needs to be inserted first, and then attach the skirt to the frame. Otherwise the screws between the NUC and the skirts may not be properly aligned.

ASUS / Intel NUC with top
removed and with HDMI flex cable connected

HDMI to
flex cable

Thunderbolt 4 / USB 4

Flex
cable

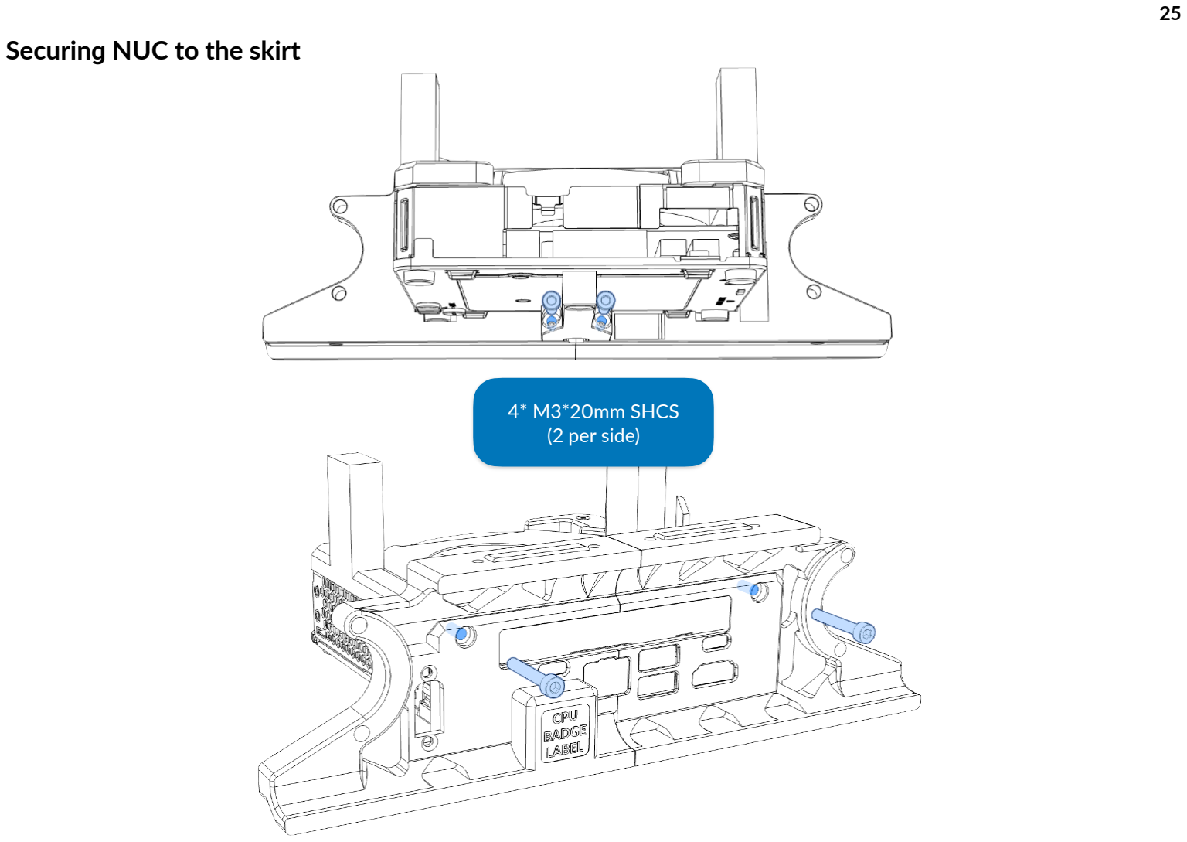
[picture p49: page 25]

25
Securing NUC to the skirt

4* M3*20mm SHCS
(2 per side)

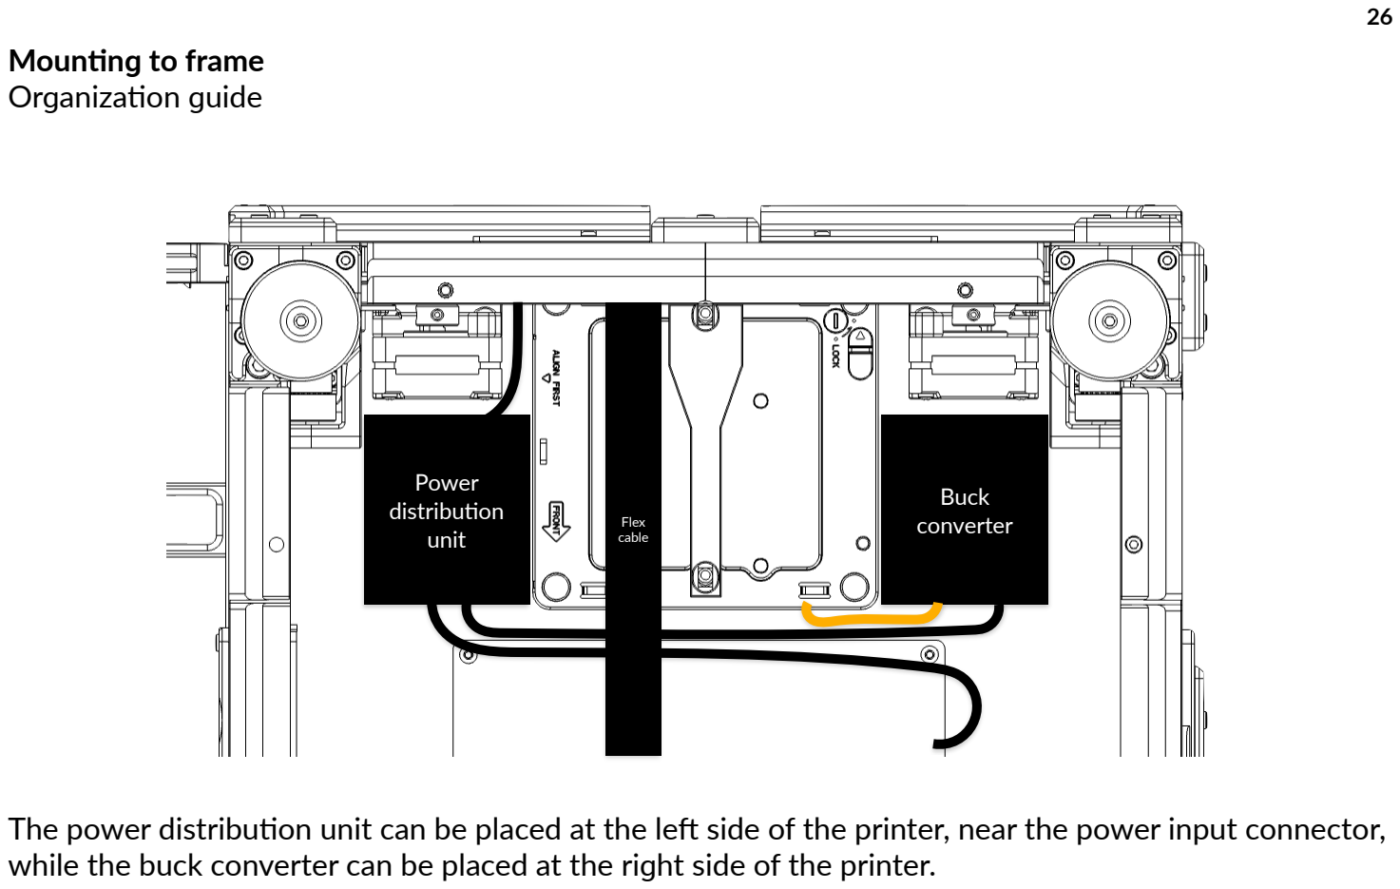
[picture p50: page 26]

26
Mounting to frame
Organization guide

The power distribution unit can be placed at the left side of the printer, near the power input connector, while the buck converter can be placed at the right side of the printer.

Power
distribution
unit

Buck
converter Flex
cable

27
The cable guide

The top-left reinforcement stud has a guide that is made specifically for the cables going out of the skirt and which prevents the cables from covering the NUC's ventilation holes. Cables that are going out from the right side should be placed or re-routed to the left side.

Cables going out

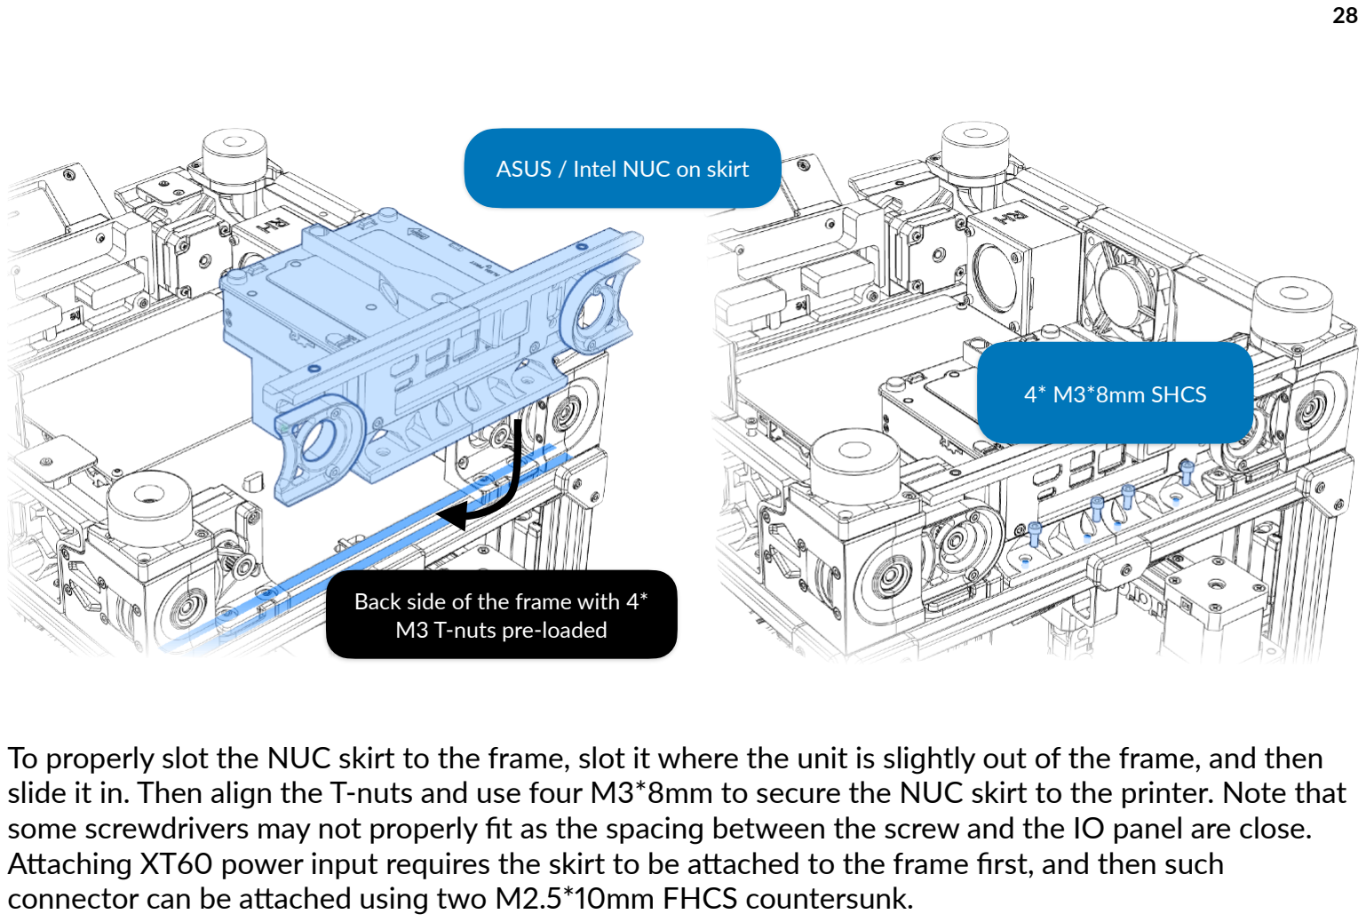
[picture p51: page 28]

28

To properly slot the NUC skirt to the frame, slot it where the unit is slightly out of the frame, and then slide it in. Then align the T-nuts and use four M3*8mm to secure the NUC skirt to the printer. Note that some screwdrivers may not properly fit as the spacing between the screw and the IO panel are close. Attaching XT60 power input requires the skirt to be attached to the frame first, and then such connector can be attached using two M2.5*10mm FHCS countersunk.

4* M3*8mm SHCS

ASUS / Intel NUC on skirt

Back side of the frame with 4* M3 T-nuts pre-loaded

29

# Hardware connection guide

You may connect non-Klipper devices to the USB 3.0 hub. Avoid connecting Klipper MCU or CAN bus unit to the USB hub that isn't intended for Klipper MCU as the hub may easily be overloaded.

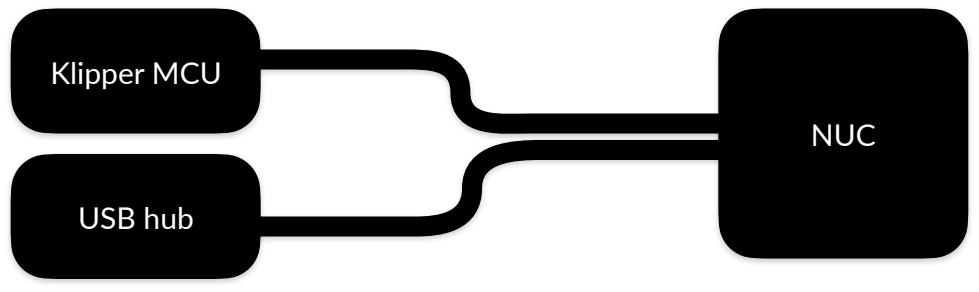
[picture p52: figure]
NUC; Klipper MCU; USB hub

You can then connect the power button from the front panel header that was extended prior. After that check to make sure the electrical work is done before covering the electronics down with the bottom panel.

30

# Software configuration

Debian Linux physical (including Ubuntu)
You can install Debian Linux (https://www.debian.org) to NUC. Virtual machine is not required. It is recommended to install the latest version of Debian or Ubuntu (https://ubuntu.com) with the desktop environment. After that, you may create own user account, setup APT server communication, choose the features. Once Debian or Ubuntu is installed, you may install KIAUH from dw-0 (https://github.com/dw-0/kiauh) if you want connivence, install Klipper, lightweight UI and probably Crowsnest through KIAUH.
Windows 11 physical + Debian Linux VM
If you are a diehard, you can install Windows 11. However a virtual machine is required to run Klipper as it is Linux Python-exclusive software. This also means requiring a Debian ISO prior install on virtual machine.
This is not recommended, (https://klipper.discourse.group/t/running-klipper-in-a-virtual-machine-vm/6325) but anyway, we are diehards
This method is not recommended as Klipper heavily relies on real-time scheduling with up to 100 milliseconds of tolerance and virtualization tends to exceed that. However, there are workarounds, (https://www.reddit.com/r/klippers/comments/1grt0wq/klipper_on_windows_wsl2_docker/) such as Process Lasso from Bitsum, (https://bitsum.com/) which allows reserving CPU cores, put programs in priorities and limit programs to only use said threads with at least three changes.
Windows Subsystem for Linux (WSL)
If the NUC has Windows installed (and licensed), you can enable this feature and install WSL, (https://documentation.ubuntu.com/wsl/stable/howto/install-ubuntu-wsl2/) install Debian / Ubuntu Linux and use KIAUH inside WSL.
VirtualBox
You can use VirtualBox if you don't want WSL, or wanted a more graphical way to adjust VM settings. However there are recommended settings that has adjusted, you need to shut the VM down in order to change:

31
- 1GB of RAM, 128MB of video memory,
- Dual- (recommended) or triple-core,
- 3D acceleration enabled,
- A bridged network adapter and a host-only adapter,
- Virtual NVMe instead of virtual SATA.

If you want to create a virtual machine from scratch:
- First, specify the name of the virtual machine, you may call it klipper.
- Then you select the ISO image (not the photo) of Debian Linux.
- And then manually specify the virtual hardware, with 1GB of RAM and dual-core.
- And specify the virtual hard disk and make sure it is somewhere around 32GB and 64GB.
- The installation steps for Debian can then be proceeded like it is in the physical machine, such as creating user accounts, choosing features, installing Klipper and its UI.

32

# Assembly complete

And we are done! If you are satisfied with such product consider tagging @officialbunny350 on Facebook or @realBunny350 on X (formerly known as Twitter) and share such product with us on Oitswilliam Pang Discord Server.

If you have enquires, problems or issues related to building or using such product, please report it on GitHub.com/Bunny350/OITSWILLIAMV2/issues and we will get on it.

Change log
- 2026-06-15 - Make the document print-compatible. Although printing is not recommended, we pretty sure not everyone enjoy reading the document through the digital screen.
- 2026-03-05 - Minor stud models renaming.
- 2026-02-13 - Add inspiration on about section.
- 2026-02-04 - Initial release

33

The whole goal of OitswilliamV2 for Voron 2 has started (2021) before Bambu Lab introduces their first ever 3D printer (2022) and then CoreXY revolution. Although OitswilliamV2 took a year just to be released, and that is 3 months behind.

Manual designed by Oitswilliam Pang. One-person operated design. www.oitswilliam.com

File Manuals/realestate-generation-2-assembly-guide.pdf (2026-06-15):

## RealEstate

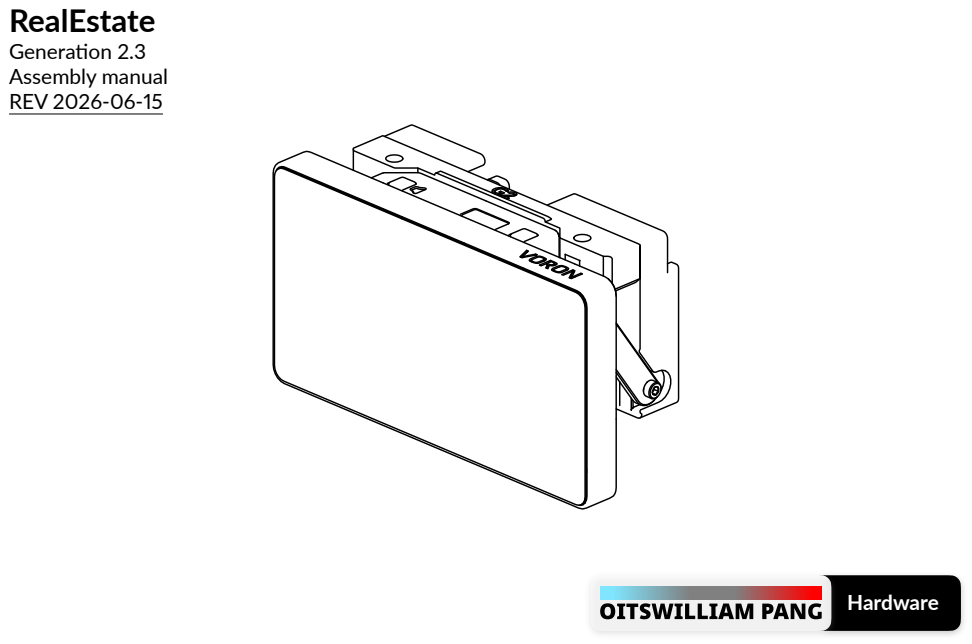
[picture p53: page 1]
Generation 2.3 Assembly manual REV 2026-06-15; Hardware

Contents • Before getting started • About RealEstate • Warnings • Contribution • Support • Part printing • Assembly • Cable preparation • Display unit • Mounting to printer • Wiring • Software configuration • Debian native KlipperScreen

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
- Windows 11 • LED • Wide button

41
42
44

# Before getting started

You are about to read the mod project assembly manual. This manual shows the assembly, wiring and configuration guide of RealEstate display for Voron Trident and Voron 2 printers.

You need to make your own micro-USB cable with four 24AWG
wires in between 30cm and 65cm ends, prepare either an endstop switch or a silent mouse switch with two 26, 28 or 30AWG
wires in between 40 and 70cm ends.

Guide and legend

- highlighted material / part
- mentioned material / part
- printable / moldable model (these includes STL, 3MF or sometimes even source files
like STEP)
The model name may not be mentioned in later pages.

Electronic parts will show their own power throughout this
assembly guide, but here are the abbreviations that will be used:
V - volt,
A or I - amp (I as amp may be used but not in this manual.),
GND - ground.
In DC,
+ - positive,
- - negative
In AC,
L - live
N - neutral
⏚, E or G - earth ground
Other abbreviations include: MCU - microcontroller unit SBC - single-board computer

# About RealEstate

RealEstate is a display unit made for Voron Trident and Voron 2. It is a freely adjustable tilting display that defines portability.

It is made using 3 parts, back unit, the arms and the screen. The arms are attached in between the back and the screen, the joints of the arms are inserted with PTFE tubes so that the friction between joints are reduced and no lubrication is required. The back of the screen has a glowing chin that is ARGB. Users can use KlipperScreen on Raspberry Pi / NUC PCs that run in Debian without any desktop environment or use Windows 11 / Debian Linux with desktop environment for experimental or limitless fun.

The current design only uses 3 types of screws that are found in Voron Design printers' BOMs, while one of it (M2*8mm BHCS or self-tapping screw) is unique to this mod.

# Warnings

Danger: risk of electric shock
- Even though you can build with this mod from start, if you want to extract the power supply that you previously have, you need to check that the mains is unplugged.
- Failure doing so which is unplugging the mains power may cause electrocution or even death, especially on regions that use 240V.
- When in doubt, please don't touch the wires connected to the power supply or SSR.

When you accept all the warnings for this project,
you can start building one.

# Contribution

Starting in November 2021, every Oitswilliam Pang projects including this will have a dedicated sources and source files for free, which makes them open-source.

If you want to contribute this project, you can visit in GitHub.com/Bunny350.

In other words, each OIWP's projects have their own licensing policies. So if you want to distribute the projects, you need to refer to their licensing policies first.

# Support

Having problems building our projects? You can contact us in Facebook or Twitter. https://www.facebook.com/officialbunny350

However, for the better experience, you can visit and then join Oitswilliam Pang Discord server and receive the community support. Please follow its rules. https://discord.gg/Cu6e9ra

If you have problems because of the project's errors or simply issues, you can submit them in GitHub. https://GitHub.com/Bunny350/OITSWILLIAMV2/issues

The manual might be updated overtime, so when you start building, or are trying to build the projects, you might need to get the latest manual if it was left for at least every three months.

Thanks for viewing the manual. Now go on the next page to build the first part.

# Part printing

Print guidelines
Each part of the model requires the following set settings, failure to match most of them may result in unexpected damages.
Bold text indicates the recommended value and italic text indicates what setting it is being changed.

Additional maker tools
To get started building the project, you must use the following tools:
- Soldering iron
Printer types FDM / FFF, SLA (non-motion parts only) or SLS | Print material: ABS, ASA or PA12 Prohibits PLA. Do not use PETG in motion or enclosing parts.
Layer height of 0.2mm Initial layer height can be 0.2mm or higher | Nozzle and extrusion width must be forced 0.4mm
1.6mm wall width Or 4 wall counts, excluding tools and jigs | Infill must be at least 40%, excluding tools and jigs
At least 4 solid bottom and top layers. | The best print speed is up to 120mm/s. The speed might be reduced by the hot end flow rate.
Supports are not required. Uncheck generate support if available. | Other settings might be depended on your printer. Follow it's warnings for proper handling.

# Assembly

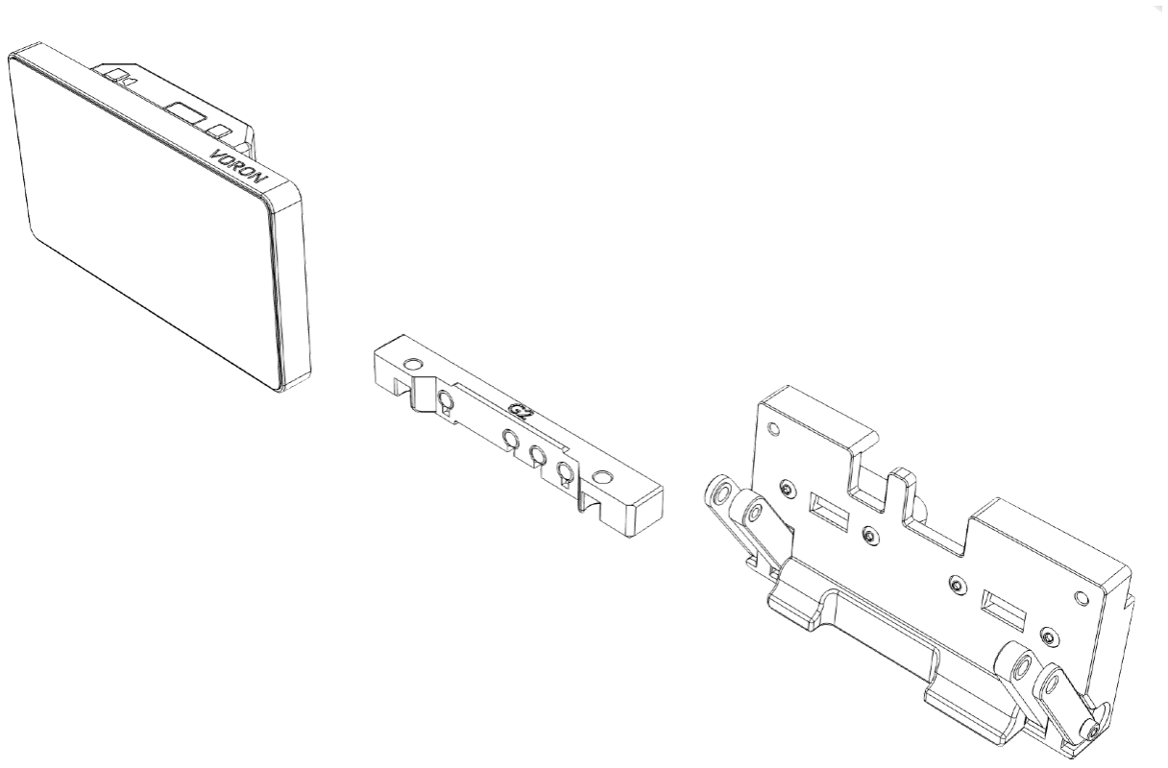
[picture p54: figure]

# Cable preparation

You need to make a micro-USB cable that has it's profile lower than the factory specified, by not installing the hard case, but with heat-shrink tube. Most factory cables do not fit into RealEstate display unit and may cause damage to the display or mount if forced. This only requires at least four 30cm 24 to 26AWG wires to power.

The cable might be extended to 50cm for 250mm spec, 55cm for 300mm spec and 60cm for 350mm spec builds. The power button needs to be approximately 40 to 75cm. This is used to turn the PC or SBC on using such button in this unit. These are for reference only. Please report these to GitHub issue if you have found the wire looking too short or long.

If you want to utilize the glowing chin, you need to wire an ARGB strip with three 50cm 24AWG wires. It might be extended to 60cm for 250mm spec, 65cm for 300mm spec and 70cm for 350mm spec builds.

This display unit also requires two HDMI to flex cable with 90 degree up on both heads. Cable included from the display never fit with this mod! 250mm spec only require 50cm flex cable while 300mm and 350mm requires 1 meter one.

If you are wiring the keys for the wide button, the easiest way to do is to wire 5V inputs by taking from the display's cable and then putting the Raspberry Pi Pico in the hatch. That way, only two wires (data wires) are exposed.

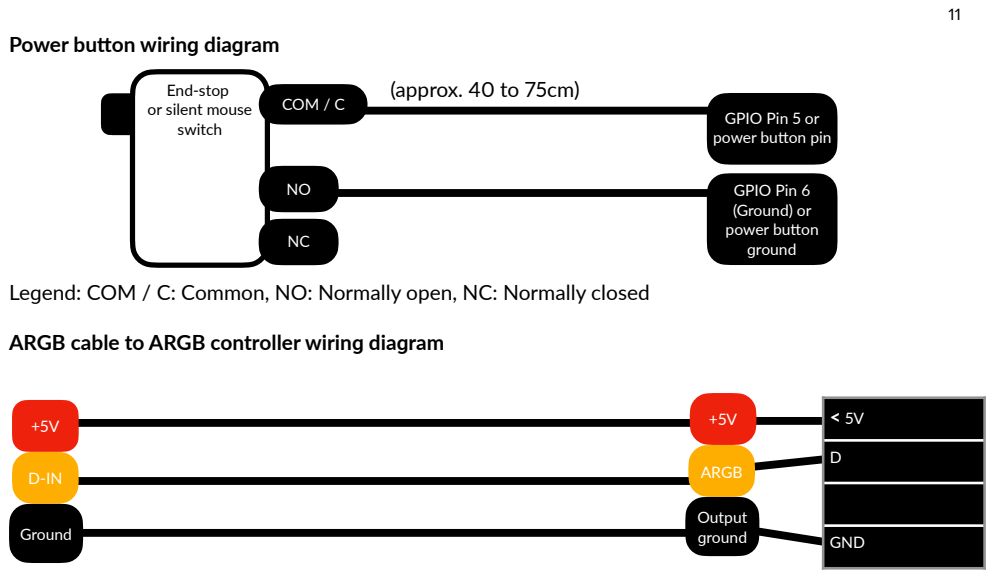
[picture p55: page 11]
GND Ground; Output ground; ARGB; COM / C; GPIO Pin 6 (Ground) or power button ground; (approx. 40 to 75cm)

Power button wiring diagram

End-stop
or silent mouse
switch

GPIO Pin 5 or
power button pin

Legend: COM / C: Common, NO: Normally open, NC: Normally closed

ARGB cable to ARGB controller wiring diagram

Wide button keys wiring diagram
Requires Gen 2.1 hatch. Requires additional 3 buttons.

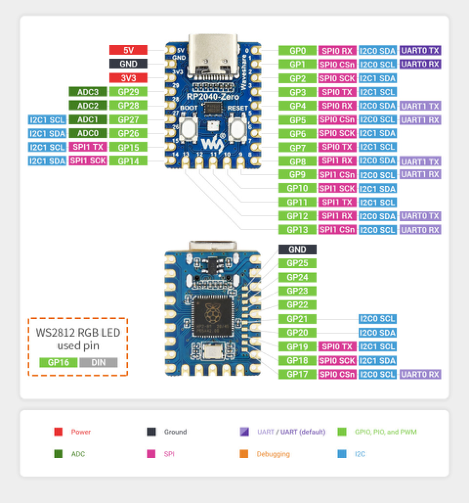
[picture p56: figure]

Mute button /
E-stop

Volume up button / Home &

pause & resume

Volume down
button / Z-tilt
& pause &
cancel

GND

WaveShare RP2040-Zero

After wiring the keys for the wide button, you may mark the volume up button with + and volume down button with - to ease assembly. You may then flash RP2040 firmware from your device. See page 44 for more details. You can see the page 17 on how to place them and tidy up wires. Please do this before assembling or upgrading, otherwise it's too late and you may need to use the software to access it's upload mode. If you have got the controller with pins, you may want to cut off 3.3V pin to prevent short-circuit. If 5V pin will not used in forever, then it's recommended to also be cut off too.

https://www.waveshare.com/
wiki/RP2040-Zero (https://www.waveshare.com/wiki/RP2040-Zero) Chin LED (Klipper firmware only)

Ground

+5V

GPIO8

GPIO9

GPIO10

GPIO11

GPIO...

# Display unit

Display body

2* Arm joint
display-arm-mount-X2.stl

4* M2*8mm SHCS /
self-tapping screws
(2 per joint)

Waveshare 5.5 inch display mount main-screen-mount-waveshare-5.5-inch-amoled.stl

Other variants of display mounts can be available via user request.

ARGB strip with
prepared cable

Display hatch
hatch-normal-microswitch.stl / hatch.stl

Power button switch
with prepared cable

M2*10mm Self-tapping
screw
(Normal microswitch
only)

For those who use silent mouse switch, a M2*10mm self-tapping screw is not needed.

This manual shows normal
microswitch / printer end-stop switch as a power button.

If the switch has a lever, you may remove the lever before inserting.

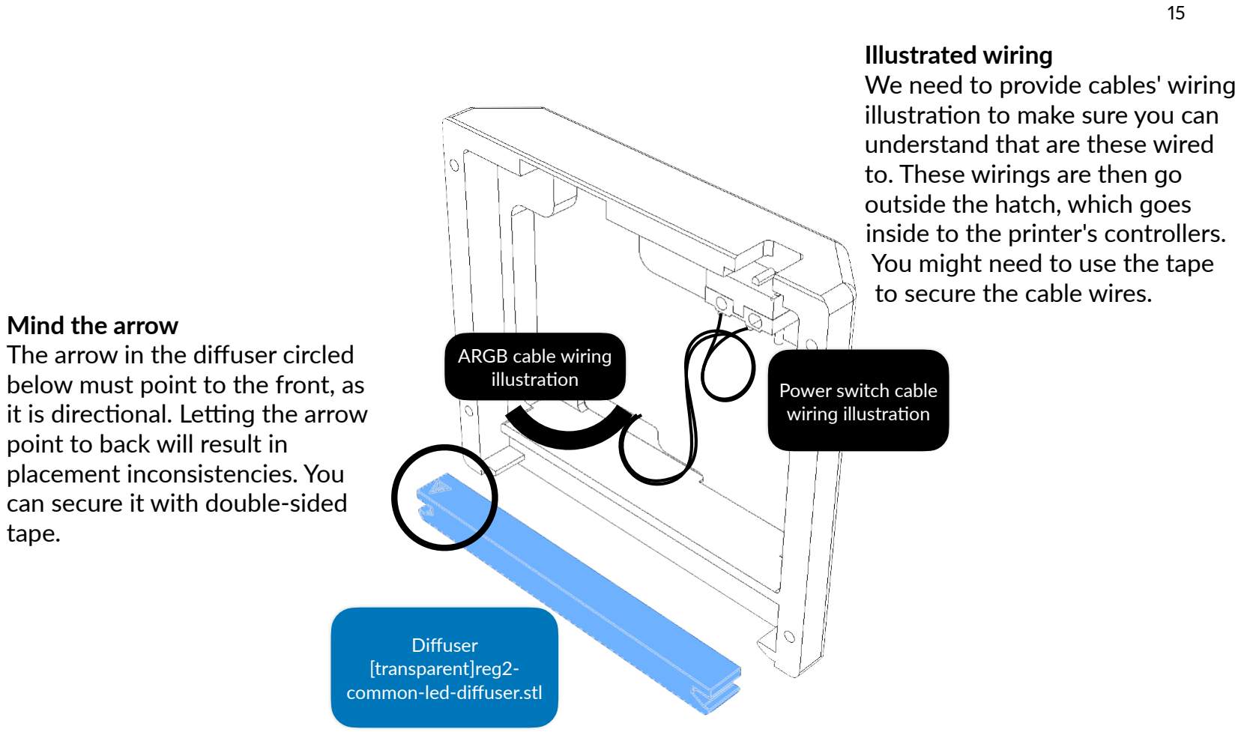
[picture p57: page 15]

Mind the arrow
The arrow in the diffuser circled below must point to the front, as it is directional. Letting the arrow point to back will result in placement inconsistencies. You can secure it with double-sided tape.

Illustrated wiring
We need to provide cables' wiring illustration to make sure you can understand that are these wired to. These wirings are then go outside the hatch, which goes inside to the printer's controllers. You might need to use the tape to secure the cable wires.

Diffuser
[transparent]reg2-
common-led-diffuser.stl

ARGB cable wiring
illustration | Power switch cable
| wiring illustration

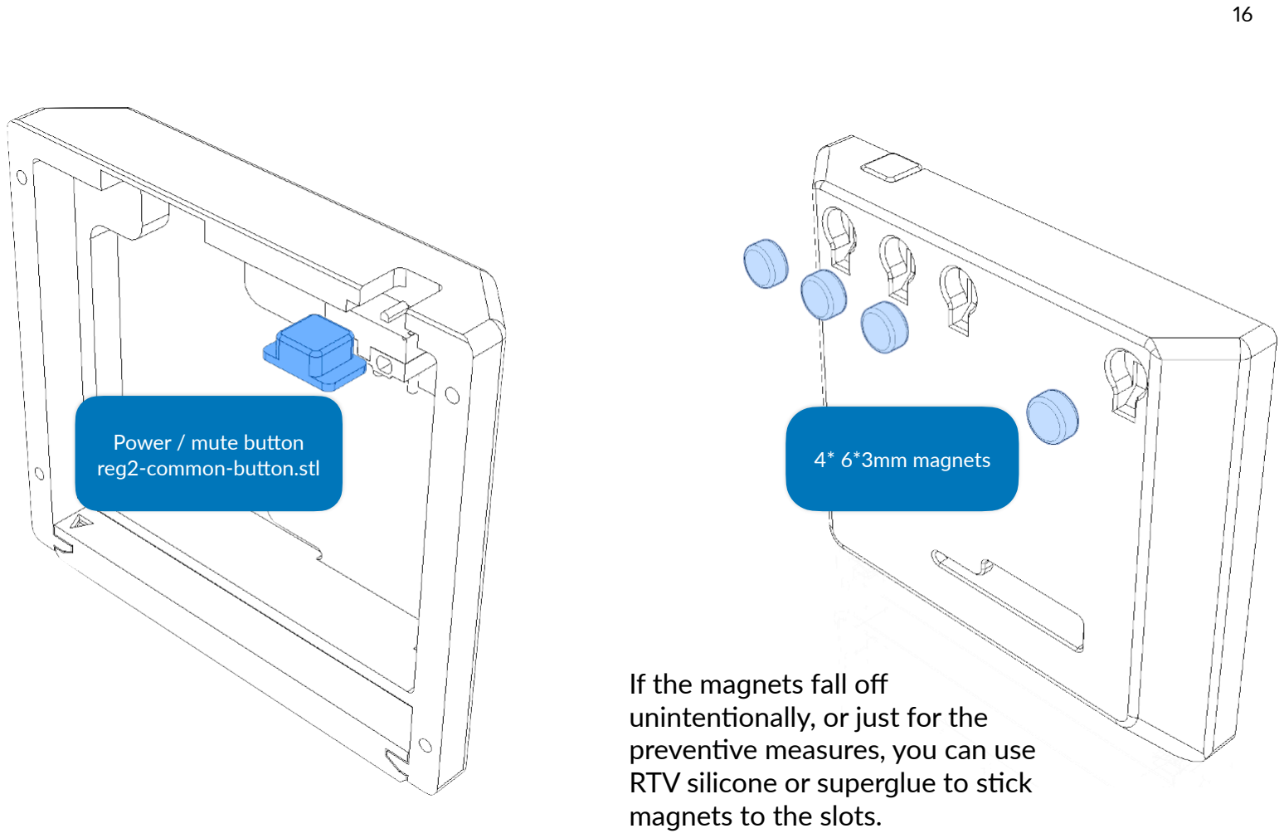
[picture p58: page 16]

4* 6*3mm magnets

Power / mute button
reg2-common-button.stl

If the magnets fall off
unintentionally, or just for the preventive measures, you can use RTV silicone or superglue to stick magnets to the slots.

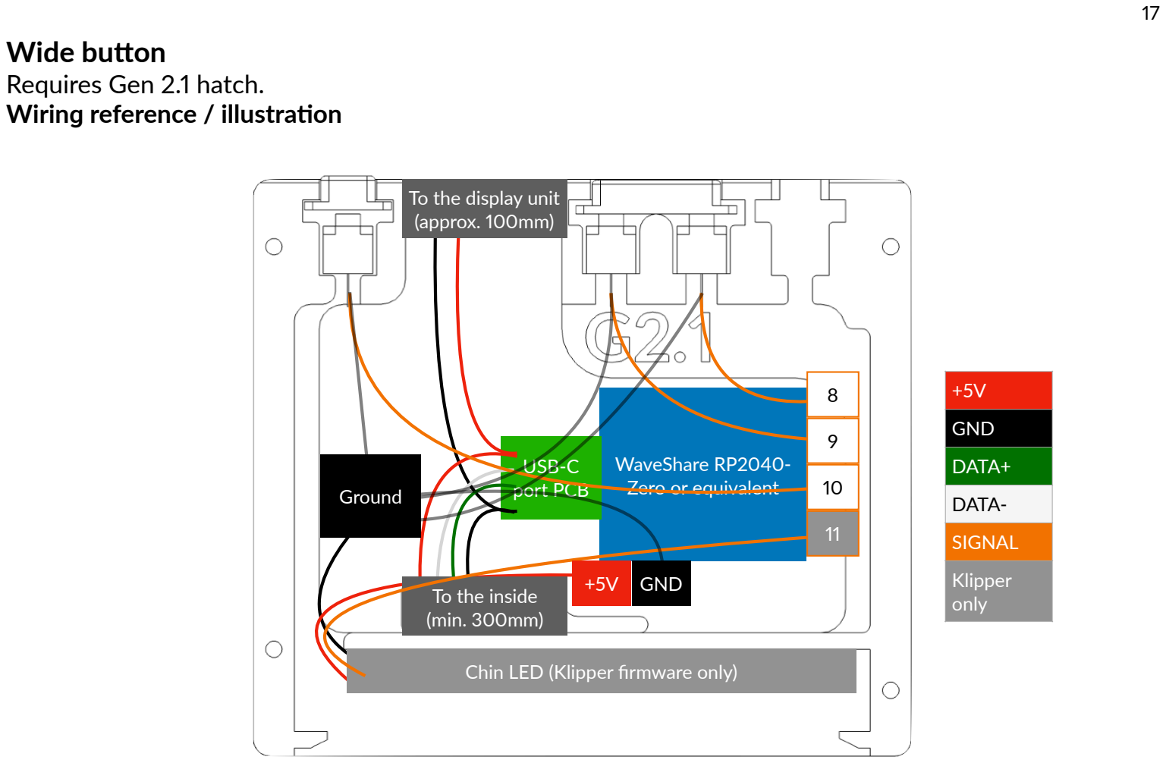
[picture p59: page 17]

Wide button
Requires Gen 2.1 hatch.
Wiring reference / illustration

+5V
GND
DATA+
DATA-SIGNAL
Klipper
only

Chin LED (Klipper firmware only)

WaveShare RP2040-
Zero or equivalent

GND

USB-C
port PCB

To the display unit
(approx. 100mm)

To the inside
(min. 300mm)

8

9

10

11

Ground

+5V

Hatch Gen 2.1 assembly

3* Silent mouse switch

Wide button
reg2-1-wide-button.stl

Power / mute button
reg2-common-button.stl

You may want to do this by removing and then reattaching multiple times per switch as the wirings are too short. You can refer to the previous page for wiring.

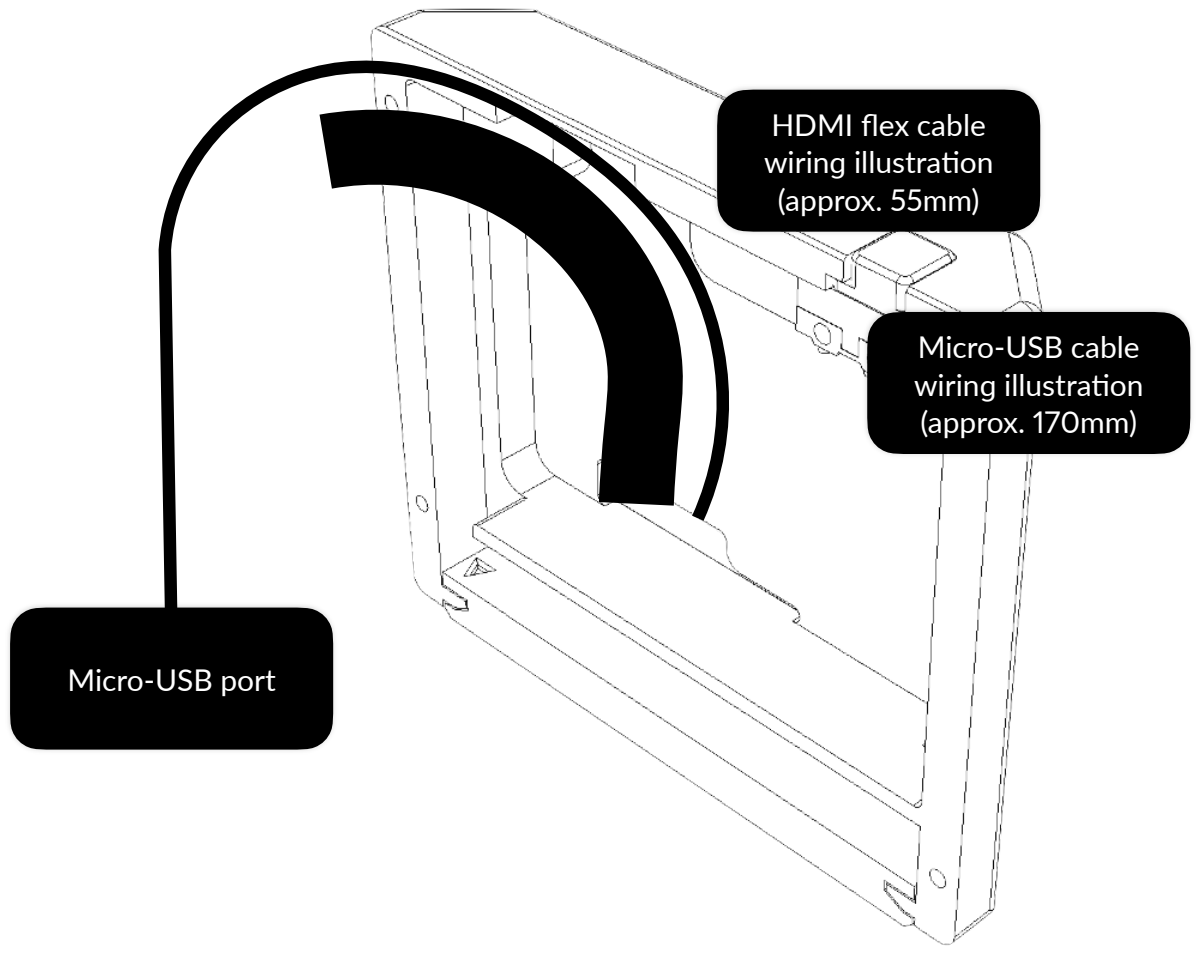
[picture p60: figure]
HDMI flex cable wiring illustration (approx. 55mm); Micro-USB cable wiring illustration (approx. 170mm); Micro-USB port

These wirings need to go from outside the hatch to the inside which is then go to the controller. Securing with tape is recommended.


Partly assembled
display hatch

Partly assembled Waveshare 5.5 inch display mount

4* M2*8mm
SHCS / self-tapping

The wirings of micro-USB cable and HDMI flex cable must then go through the display mount.


Foam tape (1mm
thick max)

Why foam tape the edge?
This is to address problem flushing the bezels of the screen and the edge of the mount. However, using foam tape that is too thick may result in screen bulging or even risk damaging the display.

Display and HDMI to flex cable connection illustration


This step requires
connecting the flex cable
to the display's HDMI
cable. First unlock by
lifting the lever, then
place the flex cable by
sliding in, and finally lock the cable by pushing the
lever. The next page will
not show the flex
connector.

Flex cable metal contact must face down relative to the adapter

HDMI to flex
cable (port
facing down)

HDMI to

Flex
cable

Please check that the display has inserted with 90 degree up HDMI to flex cable connector first.
This manual sometimes does not show the connector but you must be prepared with it first.

Waveshare 5.5 inch
AMOLED display

Micro-USB cable

This step connects the micro-USB cable to the touch & power port of the display. There is another port at the top which only powers the display, and should not be used or connected. The next page will not show the cable.


Up to approx. 30
degrees

HDMI
to flex
cable

Put the right hand close to the mount to see if the cable fits. Do not apply excessive force.

HDMI to flex cable

Be careful and slowly close the display to the mount. Do not apply excessive force or it may cause damage to the display.


4* M2.5*4mm BHCS

There are screws included in the display which uses Phillips screws, unless if you go
premium.

Middle hub preparation

2* M3 Heat set inserts

4* 6*3mm magnets

There is a trick in if the magnets attract each other, face the repelling side in the slots.
The attracting side must face front, otherwise it will not function.

Middle hub
middle-hub.stl

Back body preparation

1* or 2* Panel mount
USB port

2* or 4* M3*6mm
BHCS (2* per port)

The wires are not shown. Please refer to the wiring illustration in this manual later.

Back unit
back-assembly-screw-based-panel-mount.stl


2* M3*6mm BHCS

Tilt bump
reg2-common-tilt-bump.stl
The tilt bump will have the securing holes directly tapped by fasteners.

Hinge arm attachment

Hinge arm B (heat-set side) hinge-arm-b.stl (left) hinge-arm-b-mirror.stl (right); 2* M3 Heat set inserts

Please do not a

ttach heat set
inserts into the spacing sides. Check that the spacing is facing the opposite from the heat set insert.

This step is repeated on the right-hand side.

Hinge joint assembly - display side
This procedure uses 3mm ID 4mm OD PTFE tube, do not use the tubes that are in 2.5mm ID or the screw will not properly fit.

2* ~9.5mm Reverse Bowden tube (3mm ID 4mm OD PTFE tube); Partly assembled display unit

Identifying sides of the arm joint
This part has different sides that are being jointed on respective components, in this part, the properly rounded end (the right side) goes to the display, while the oddly rounded end (the left side) will go to the back body.

This applies on both joint A (hinge-arm-a.stl and hinge-arm-a-mirror.stl) and B (hinge-arm-b.stl and hinge-arm-b-mirror.stl), which are screw-secure sides and heat set sides respectively. If these sides are reversed, it may not function properly, or even cause damage.


Display unit

Please check that the spacings are facing at the screw holes. The properly rounded sides must not mount back body.

Back unit

Properly rounded ends

2* ~9.5mm Reverse
Bowden tube (3mm ID
4mm OD PTFE tube)

Hinge arm B (heat-set side) hinge-arm-b.stl (left)
hinge-arm-b-mirror.stl (right)

Le

f

Right


Hinge arm A (screw-securing side)
hinge-arm-a.stl (left)
hinge-arm-a-mirror.stl (right)

## Lef

These steps are repeated on the right-hand side.

2* M3*12mm BHCS

Display to back body cabling illustration

power (approx. 60mm)

To the inside of the printer

HDMI flex cable | USB touch, ARGB and

Back unit +
display unit

2* M3*16mm BHCS

Cables from
display

Middle hub


Mounting to printer

2* M5*10mm BHCS

This step assumes the display placement is front-center.
The placement of T-nuts or hammer nuts are at the bottom of extrusion.
This step does not show the skirt assemblies.

M5 2020 T-nut /
hammer nut

Wiring diagram; ARGB LED; Ground; ARGB or free pin; Power button; GPIO Pin 6 (Ground) or power button ground; (approx. 40 to 75cm)

MCU or ARGB
controller

HDMI
connected with
adapter and free
USB or hub

SBC / Mini PC

HDMI cable +
touch and power

GPIO Pin 5 or
power button pin

Volume /
function keys
from Pi Pico

You may need to tidy up the
cables after wiring.

Free USB or hub

# Software configuration

Debian native KlipperScreen

Set up the display
You may need to set up the display to make sure it is displaying correctly.
Please visit https://klipperscreen.readthedocs.io/en/latest/Hardware/ for more accurate information. Basically, the display RealEstate uses is in portrait by default, which is a problem. To address the issue, you need to manually rotate the screen to landscape.

After this code has been pasted to /usr/share/X11/xorg.conf.d/90-monitor.conf, you need to restart KlipperScreen

Section "Monitor"

Identifier "HDMI-0"

Option "Rotate" "right"
# This will address the display's portrait mode by default problem

Option "PreferredMode" "1920x1080"
EndSection

If the touch panel isn't register correctly after completing the first step, you need to also rotate the touch panel to the correct orientation. First, find the touch controller.

If you have found the touch controller of the display, execute this command; remember to change the device name.

If the touch panel is navigating correctly, you also need to make the change permanent, this is specially needed in case of host restarts. In /etc/udev/rules.d/51-touchscreen.rules , you need to add a line containing such code, and remember to change the device name.

If the code above did not resolve the touch panel issue, you may head to /usr/share/X11/xorg.conf.d/ 40-libinput.conf and add the following code:

DISPLAY=:0 xinput set-prop "<device name>" 'Coordinate Transformation Matrix' 0 1 0 -1 0 1 0 0 1

ACTION=="add", ATTRS{name}=="<device name>", ENV{LIBINPUT_CALIBRATION_MATRIX}= 0 1

This is then needs to be saved and the host needs to be restarted.

Windows 11
To rotate the screen and touch panel in Windows, run Settings, then select display, find the display resolution section and set the display orientation to portrait (flipped)

The display was in portrait mode by default which result in Windows showing it as landscape even though it is in portrait orientation.

Section "InputClass"
Identifier "libinput touchscreen catchall" MatchIsTouchscreen "on"
MatchDevicePath "/dev/input/event*"
Driver "libinput"
Option "TransformationMatrix" "0 1 0 -1 0 1 0 0 1"

EndSection

Klipper LED
If you are using dedicated RGB controller, this section is not required.
If you want to use RealEstate glowing chin LEDs with Klipper MCU, you can use the following code:

Once assigned, the LEDs still didn't have animations or reflect status yet, you can then add this code which you can customize.

Add new Neopixel feature
Assign pin (you need to change to pin connected from) Chain count (number of LEDs chained)
Color order (not required if using default)
Emission value on start-up

SET_LED LED=realestate_chin RED=<value> GREEN=<value> BLUE=<value> [INDEX=<index>]

If you have Klipper LED Effect (https://github.com/julianschill/klipper-led_effect) installed, you can add the commands below. More information can be found here. (https://github.com/julianschill/klipper-led_effect/blob/master/docs/LED_Effect.md) This is an example of the chin working. In the config file, add this sample line:

[led_effect realestate]; autostart:; true; frame_rate:; leds: neopixel:realestate_chin layers: gradient 0.5 1 top (1.0,0.0,0.0),(0.0,1.0,0.0),(0.0,0.0,1.0)

You can then check to make sure the gradient plays automatically after restart. If you want to stop the animation, you can execute SET_LED_EFFECT EFFECT=realestate STOP=1 in Klipper console. If you want to re-run such animation, you can execute SET_LED_EFFECT EFFECT=realestate in Klipper console.

If you are satisfied with such feature, you can rename realestate and tinker with your settings.

Wide button
Requires Gen 2.1 hatch and CIrcuitPython in RP2040.

This requires a Raspberry Pi RP2040-based MCUs that is not running Klipper but rather as a media controller. We recommend WaveShare RP2040-Zero or equivalent.
This feature uses Adafruit CircuitPython, an easy-to-use coding firmware, and Adafruit HID library. You can get these from CircuitPython (https://circuitpython.org/board/raspberry_pi_pico/) (may select language) and the library GitHub repository (https://github.com/adafruit/Adafruit_CircuitPython_HID) there for the latest version. It may come outdated in OITSWILLIAMV2 repository.

You may need to do the following steps:
1. Get these files above and from OITSWILLIAMV2/Config/Non-Klipper/RealEstate repository.
2. Reboot the Pi Pico in bootloader mode by pressing reset and boot buttons, and then drop the CircuitPython firmware file to Pico's drive in bootloader mode, in order to flash it's firmware.
3. Drop boot.py, code.py and the library into Pico's drive that is later called CIRCUITPY.
You may copy the Adafruit CircuitPython HID into the drive's lib folder.
Note: if you did not put boot.py on this drive, the drive mass storage will keep showing up, but if you don't put code.py, it will not function as intended, and you will no longer access it's contents until you use a coding software like Mu Editor or Thonny.
4. Reboot Pico by pressing the reset button, or power-cycle by unplug-then-re-plug.
5. Test the three buttons, down, up, mute, and then press-and-hold mute, and then down and up. You must expect it to raise up volume, drop down volume, mute, and then increase and decrease brightness.

Once these are done, you can continue assembling the hatch in the page 17.

Function keys
Requires Gen 2.1 hatch and Klipper firmware in RP2040.

If you want to use RealEstate G2.1 with Klipper MCU, you may refer to OITSWILLIAMV2/Config/ RealEstate.

You may flash the RP2040 firmware in bootloader mode before assembling the hatch in the page 17.

The following changes that were made to adapt with Klipper:
- Mute button will be replaced with emergency stop button,
- Volume down button will be replaced with home, pause and resume,
- And volume up button will be replaced with Z-tilt, pause and stop.

You can change each button's behavior by changing their press Gcode.

Buttons

Volume up
Increase brightness**

Volume down
Decrease brightness**

Mute / brightness* switch Emergency stop***; Z Tilt / pause / stop printing***; Home / pause / resume***

* Brightness control only applies to future models of display. Displays that do not have on-computer brightness control may not work as intended.
** Must press the mute switch to access this function.
*** Klipper function. You can change depending on your needs. Conflicts with volume keys.

# Port connection guide

RealEstate display mount comes with up to two USB ports for extended connectivity. With prior generations, including G1, the ports are straightened to the mount, but since these are either inaccessible or too difficult to access, even with instructions properly followed, on G2.3, the ports are tilted and pushed slightly up so that the USB devices and thumb drives can be connected easily.

# Assembly complete

Now you can unlock the superpowers of unusual usage of devices. However this manual does not include unusual guides and troubleshooting guides. This means, if you have problems with this mod, you need to head to GitHub.com/Bunny350/OITSWILLIAMV2/issues, join and message in Oitswilliam Pang Discord server or message @officialbunny350 on Facebook.

You can also make content with RealEstate display unit, just because, you can.

# Change log

- 2026-06-15 - Introduce generation 2.3. This generation adjusts the back unit to have USB ports tilted for easier port connections. This change replaces G2.0 back unit. Rename "volume buttons" to wide button.
- 2026-01-15 - Minor changes that address text placement. Add file names to parts. Add guide and legend before getting started. Remove support for Windows 10. Add the port shape on page 25. Reword the vaguely defined "required tools" to additional maker tools. Changed some descriptions to page 5. Change change log date formatting to reflect it in the first page. Update front page with vector. Add hardware logo next to Oitswilliam Pang.
- 2024-05-25 - Change domain from bunny350.github.io to the redirected www.oitswilliam.com.
- 2023-10-01 - Added materials related to generation 2.1 of such part, including the hatch and the wiring of its hardware. This change does not replace G2.0 hatch. Changed font to Lato OIWP.
The following logs which is prior to Gen2.1:
- 2023-07-14 - Rewording, including renaming "heat seat" to the proper name.
- 2023-04-06 - Added information about the unit's wiring and the information dedicated to the lever removal of the printer endstop switch.
- 2023-03-08 - Initial release

Manual designed by Oitswilliam Pang. One-person operated design. www.oitswilliam.com

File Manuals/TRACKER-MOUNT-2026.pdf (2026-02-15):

Tracker mount for standard Voron printers - installation guide (AirTag mount G4, Galaxy SmartTag2 mount G2)
Prerequisites - the unit needs to be attached to a 60mm fan mount that has 3mm of thickness in-between the shroud and the fan (or the unit and the

mount).; 4* M3*6 BHCS; Tracker mount back tracker-mount-airtag-back-g4.stl (AirTag) tracker-mount-smarttag-back-g2.stl (Galaxy SmartTag2); 4* M3*5*4 heat set inserts; Tracker mount back; 60mm fan mount; Skirt

The mounting bracket needs to be attached to one of the fan mounts prior installation of the tracker. Check the arrow, it should point to top after installation, or the screws mounting to the frame. The back of the unit should face to the internals.

## Tracker attaching

AirTag-specific; Galaxy SmartTag2-specific; nut.stl; Main unit; (AirTag); (Galaxy SmartTag2); Item tracker AirTag / Galaxy SmartTag2

Tracker mounting
bracket
tracker-mount-airtag-
bracket.stl

Tracker mounting nut
tracker-mount-smarttag-

Turn the bracket clockwise to secure the AirTag.

Turn the nut clockwise to secure SmartTag2.

tracket-mount-airtag-main-g4.stl

tracker-mount-smarttag-main-g2.stl

Unit mounting; Tracker on unit; Tracker mount back on fan; mount; Click

You will hear double-clicking when the unit is being secured.

## Instructional stickers

You can use the instructional stickers provided here, (https://github.com/Bunny350/OitswilliamV2/tree/For-Voron-2.4/Media/Tracker%20instructional%20sticker) you should choose according to your item tracker. This version is prepared for paper cutting machines.
PDF version is also available, inside the STL model folder. (https://github.com/Bunny350/OitswilliamV2/tree/For-Voron-2.4/Models/STL/Tracker%20mount/TRACKER-COMMON-FOR-VORON-ready-to-print.pdf) PDF file is intended for hand-based cutting, and you may need to manually set specific page when doing that.

## Removal guide

Turn the unit counter-clockwise to remove it. You will hear clicks during removal.


For AirTag version, unless if the part is imperfect, you can remove the battery of the tracker without the unit disassembled.

You can turn the bracket or the nut counter-clockwise to allow removal of the tracker.


2026-02-15 | TRACKER-MOUNT-2026

For other questions or problems, please visit oitswilliam.com/support. To flag issues on this manual, you can report them on GitHub.com/Bunny350/OitswilliamV2/issues.

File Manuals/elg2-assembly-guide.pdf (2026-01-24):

Exhaust Lite Generation 2 Assembly manual REV 2026-01-24; Hardware

# Contents

- Before getting started
- About Exhaust Lite
- Warnings
- Contribution
- Support
- Part printing
- Assembly
- Inner cover
- LED Back
- Unit body
- Filament runout sensing (BSPP model only)
- Inserting the Bowden tube coupler
- Attaching the body unit
- Attaching inner Bowden tube

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
- Webcam installa

tion
- OV5640 laptop webcam • Mini webcam
- Cable cover • Webcam wiring • Filter cartridge • Slotting the filter • Attaching the back Bowden tube
- Vent port
- So

ftware con

figura

tion

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
# Before getting started

You are about to read the mod project assembly manual.
This manual shows the assembly, wiring and configuration guide for Exhaust Lite Gen 2 for Voron Trident and Voron 2 printers.

Guide and legend

- highlighted material / part
- mentioned material / part
- printable / moldable model (these includes STL, 3MF or sometimes even source files
like STEP)
The model name may not be mentioned in later pages.

Material

Material

Electronic parts will show their own power throughout this
assembly guide, but here are the abbreviations that will be used:
V - volt,
A or I - amp (I as amp may be used but not in this manual.),
GND - ground.
In DC,
+ - positive,
- - negative
In AC,
L - live
N - neutral
⏚, E or G - earth ground
Other abbreviations include: MCU - microcontroller unit SBC - single-board computer

# About Exhaust Lite

Exhaust Lite is a shrunk-down version of exhaust unit that was made for portability. It uses activated charcoal pellets to purify VOCs made by melting filament. It can last for up to 3 months before it needs to be replaced or reactivated.

Exhaust Lite Gen 2 uses 4010 axial fan and supports external venting hose with 38mm of diameter. This makes print ventilation easier.

Exhaust Lite has array of LEDs called LED back to show the printer stats. It also allows mounting webcam inside the printer.

# Warnings

Danger: risk of electric shock
- Even though you can build with this mod from start, if you want to wire, or re-wire, you need to make sure and check that the mains is unplugged.
- Failure doing so which is unplugging the mains power may cause electrocution or even death, especially on regions that use 240V.
- When in doubt, please don't touch the wires connected to the power supply or SSR.

Warning: electrostatic discharge
- You should be wearing with an anti-ESD strap that is connected to earth ground before disassembling certain components.
- You may stop and not wear such strap when accessing high-voltage components.

# Contribution

This project is a part of OITSWILLIAMV2 mod pack. If you want to contribute this project, you can visit GitHub.com/Bunny350/OITSWILLIAMV2.

In other words, each Oitswilliam projects have their own licensing policies. So if you want to distribute the projects, you need to refer to their licensing policies first.

# Support

Having problems building our projects? You can contact us in Facebook or Twitter. https://www.facebook.com/officialbunny350

However, for the better experience, you can visit and then join Oitswilliam Pang Discord server and receive the community support. Please follow it's rules. https://discord.gg/Cu6e9ra

If you have problems because of the project's errors or simply issues, you can submit them in GitHub. https://GitHub.com/Bunny350/OITSWILLIAMV2/issues

The manual might be updated overtime, so when you start building, or are trying to build the projects, you might need to get the latest manual if it was left for at least every three months.

Thanks for viewing the manual. Now go on the next page to build the first part.

# Part printing

Print guidelines
Each part of the model requires the following set settings, failure to match most of them may result in unexpected damages.
Bold text indicates the recommended value and italic text indicates what setting it is being changed.

Before assembly
To get started building the project, you may use the following tools:
- Soldering iron
- Heat shrink tubes (including red, black, green and yellow, or labeled), at least 1mm diameter
- Superglue (on attaching vent port and magnet)
- Marker and utility knife or specifically made splicer / cutter (for splicing the Bowden tube)
Printer types FDM / FFF or SLS SLA only for parts with no heat-seat parts | Print material: ABS, ASA or PA12 Prohibits PLA.
Layer height of 0.2mm Initial layer height can be 0.2mm or higher | Nozzle and extrusion width must be forced 0.4mm; if using 0.4mm nozzle
1.6mm wall width Or 4 wall counts, excluding tools and jigs | Infill must be at least 40%, excluding tools and jigs
At least 4 solid bottom and top layers. | The best print speed is up to 120mm/s. The speed might be reduced by the hot end flow rate.
Supports are not required. Uncheck generate support if available. | Other settings might be depended on your printer. Follow the print material warnings for proper handling.

# Assembly


# Inner cover


For covers without built-in webcam or webcam attached outside such cover, use exhaust-lite-chambercover.stl, otherwise if you want to install webcam into such cover, use exhaust-lite-chamber-coverwebcam.stl.

Chamber cover
exhaust-lite-chamber-cover.stl / exhaust-lite-chamber-cover-webcam.stl

Adhesive tape

VT / V2 Back panel

# LED back

Wiring reference
This page shows for strips with 60 LEDs per meter. If this differs like for example the strip has less or more LEDs per meter, you may use approximate dimensions and you may need it longer or shorter, appropriately.
In this manual, we will guide it's wiring, then wire before attaching, which is then done by attaching the printed part first.

7pc. LED
(~112mm)

6pc. LED
(~96mm)

6pc. LED
(~96mm)

7pc. LED
(~112mm)

From / To
MCU

Left LED

Top-left LED
6pc. LED
~96mm

Right LED

+5V

DIN

GND

+5V

DOUT

GND

+5V

DOUT

GND

Left side LED
7pc. LED
~112mm

G
N
D

D
IN

+
5V

Screw
thread

24AWG silicone
wire

+5V: approx. 25mm
DOUT: approx. 18mm
GND: approx. 10mm

Right LED

Top-right LED
6pc. LED
~96mm

Left LED

DIN

GND

+5V

DIN

GND

+5V

DOUT

GND

Right side LED
7pc. LED ~112mm

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
Screw
thread

24AWG silicone
wire

G
N
D

D
IN

+
5V

MCU ground or
5V PSU ground

Free signal / LED pin
MCU 5V or 5V
PSU

+5V

+5V: approx. 25mm
DOUT: approx. 18mm
GND: approx. 10mm

Ending with approx. Wire (print vol.) / 350mm (150mm) 450mm (250mm) 500mm (300mm) 550mm (350mm)


Center

Left LED | Right LED

+5V

DOUT

GND

+5V

DIN

GND

24AWG silicone
wire

Wires approx. 48mm
Wires may be stacked. If certain wires are stacking, then they should still be okay.

LED exhaust spacer
led-wire-exhaust-spacer-4mm.stl / led-wire-exhaust-spacer-6mm.stl

Mount installation
T-nuts must be preloaded first. | 1X M5 T-nut (Center)

LED back internal units
led-mount-lefthand.stl +
led-wire-exhaust-spacer-4mm.stl (for 4mm)/
led-wire-exhaust-spacer-6mm.stl (for 6mm) +
led-mount-righthand.stl

Back of Voron
Trident / V2

8X M3 T-nuts / wing
nuts (4 per side)

You may rely on the
total thickness of the
back panel. If the panel
has total thickness of
4mm then use led-wireexhaust-spacer-4mm.stl,
or if the panel has total
thickness of 6mm, then
use led-wire-exhaust-spacer-6mm.stl. This
procedure will continue
on the diffusers.

8X M3*6 BHCS (4
per side)

Back panel


Assembled LED strip
unit

Left LED diffuser
[transparent]diffuser-lefthand.stl (for 4mm) /
[transparent]diffuser-lefthand-6mm.stl (for 6mm)

6X M2*10mm self-tapping screws
(3 per side)

Right LED diffuser
[transparent]diffuser-righthand.stl (for 4mm) /
[transparent]diffuser-righthand-6mm.stl (for 6mm)

# Unit body

Preparation

6X M3*5*4 heat set
inserts

Main unit body
main-body.stl

Hose attachment magnet
Absolute directions (north or south) doesn't matter as long as they attract each other for single-unit use, otherwise, if it or the hose is being used across somewhere around the room, building or the world, you may stick the magnet with it facing south to the unit side. You may use a U-shape magnet or a bar magnet with color-code and / or north and south letters.
The attachment cutout must be coated with or with at least a drop of superglue.


Installing filament runout detector
1/8" BSPP only. Only needed if runout sensing from ELG2 is required. May not be used if other runout sensing nearer between the hot-end is attached.

In-model support
material

MR85 ball bearing
1/8" BSPP adapter with
runout detector
8-1-bspp-adaprunout.stl

M5*20 to 30 BHCS

MR85 ball bearing

Microswitch wiring and installation

D2F Microswitch

The microswitch lever
must be removed before
proceeding this step. To
remove the lever, you
can press the thin side of
the lever with pliers and
then pull it. | M2*10mm BHCS or
| self-tapping screw
NO | COM

GND

Runout
signal
Ending with
approx.
350mm (150mm)
450mm (250mm)
500mm (300mm)
550mm (350mm)

Tidying up wires


The runout sensor wires must be tucked and placed on the lefthand cutout where the left arrow is pointing at.


Inserting the Bowden tube coupler
You may use the wrench if hand-tightening is too weak.

Bowden tube coupler

Bowden tube adapter
1/8" BSPP adapter with runout detector or
8-1-bspp-adapter.stl /
pc4-m6-adapter.stl

10 or 15mm

Exhaust fan installation

4010 fan

Main body

The fan exhaust must be facing back / exposed and the fan wires must be facing bottom.


Wire feeding
The wire from the fan to MCU must be tucked and then covered by 1mm foam tape or covering tape.

To MCU

1mm Foam tape /
covering tape Ending with
approx.
350mm (150mm)
450mm (250mm)
500mm (300mm)
550mm (350mm)

LED unit
Optional step, might be used if the environment is too dark most of the time.
This unit uses a strip that has 144 LEDs per meter as standard, but you can use the strip with 60 LEDs per meter. Otherwise you may use two OIWP BabyDrone back LED units.

Heat shrink guiding

LED unit strip
5 pc. LED ~35mm (144 pc/m) / 2pc. LED ~31mm (60 pc/m) / 2 set BabyDrone back LED units

+5V

DIN

GND MCU ground or
5V PSU ground

Free signal / LED
pin

MCU 5V or 5V
PSU

Wire approx.
360mm (150mm)
460mm (250mm)
510mm (300mm)
560mm (350mm)

LED unit strip

+5V

DIN

GND
GND

ARGB

+5V

Colored heat shrink or
labeled heat shrink

GND

ARGB

+5V

To MCU

Attaching the diffuser to the unit body

LED strip

LED diffuser
[transparent]led-unitdiffuser.stl

LED unit body
led-unit-body.stl

2X M2*10mm self-tapping screws

Do not crimp the connectors just yet! You may head to the next page without crimping these connectors.


Webcam cable and chamber LED wires preparation Reference

To SBC To MCU

LED unit

Connector end

The wires may be tucked later.

Attaching the body unit

Partially assembled
ELG2 body unit

M5*40mm SHCS

Pay attention to the
wires between the
LED units.


Attaching the reverse Bowden adapter

Reverse Bowden
adapter

M3*20mm SHCS

Attaching inner Bowden tube
Preparation
You may need a spare tube if your tubes are too short. You can refer to the total tube length if you are planning to replace the Bowden tube.

Inner tube length
~380mm (150mm)
~480mm (250mm)
~530mm (300mm)
~580mm (350mm)

Back tube length
~370mm (150mm)

~420mm (250mm)
~455mm (300mm)
~470mm (350mm)

Total tube length
[Tube length] (printer print vol.) ~750mm (150mm)
~900mm (250mm)
~985mm (300mm)


Attaching the inner tube

Inner Bowden tube

Chamber cover

Toolhead

Inner screws mounting

Without LED unit | With LED unit
M3*10mm FHCS | LED unit + M3*16mm SHCS

OR

# Webcam installation

OV5640 laptop webcam
Preparation

inserts

In-model support base | 2X M3*5*4 heat set

Attaching the OV5640 laptop webcam

OV5640 laptop webcam

Some OV5640 webcams may
come with back adhesive which you can use it to secure the webcam to the mount while the unit is being assembled.

Note: if the filaments are too small, you may need to remove them while mounting to the exhaust unit. If the filaments are too big they cannot insert, this step should be skipped.

Wire feeding and guiding to OV5640 laptop webcam mount

Webcam cable; To SBC

The model comes with the cutout that is just for wire guiding. To use it, you must connect the webcam cable first, and then guide the wire before and after installation.

Mounting converted OV5640 laptop webcam to ELG2

Turn the webcam angled, at around 20 degrees, then place it with the mounting holes inside, and then turn back for screwmounting. The right screw is for mounting the webcam against the cover and the left one can be attached with the front cover.

Converted OV5640
laptop webcam

Chamber cover

M3*8mm SHCS


Attaching OV5640 laptop webcam cover

M3*8mm SHCS
OV5640 camera front
cover

Partially assembled mini
webcam with screw mount

Mini webcam mount mini-webcam-backside.stl; 2X M3*5*4 heat set inserts

Mini webcam
Preparation

Feeding cable to mini webcam mount

Un-feed the cable from the webcam cutout of ELG2 cover, then pass through the cable to the mount while the cable's webcam connector is still in the body unit.

Attaching the mini webcam to the mount


Connect the webcam cable to the mini webcam, then use the
webcam's adhesive.

Mini webcam; Apply pressure

When attaching the webcam, it needs to be aligned righthand. Otherwise, the front cover will not place properly.

Attaching the mini webcam cover

Mini webcam front
cover

Chamber cover

2X M3*8mm SHCS


Attaching the mounted mini webcam to chamber cover

# Cable cover

There are 4 models for 2 variants of panel thickness (4mm and 6mm) and the maximum space thickness (10mm and 15mm). You can choose the thinner version (10mm) for better aesthetics or thicker version (15mm) for extended cabling space. You may remove the normal middle panel clip of the right side of the back panel.
Tucking wires

Variants:
- cable-cover-unified-15MM-4mm (4mm panel, 15mm total thickness)
- cable-cover-unified-10MM-4mm (4mm panel, 10mm total thickness)
- cable-cover-unified-15MM-6mm (6mm panel, 15mm total thickness)
- cable-cover-unified-10MM-6mm (6mm panel, 10mm total thickness)


Attaching the cable cover
T-nuts must be preloaded.

Cable cover

2X M3 T-nuts / wing
nuts (1X if replacing
from normal middle
clip)

You may want to place it angled, and tuck wires back in. You can move it up or down when T-nuts need to be aligned.

Back of Voron
Trident / V2

Once that's done, you should feed the wires to the controller units.

# Webcam wiring

Wirings are illustrated
Unless if you are using a cable that's long enough, this might be a step that may take some time.

Simon Eugster – Simon / ?! 19:02, 7 January 2008 (UTC) -Own painting/graphic, CC BY-SA 3.0, https://

# Filter cartridge

Preparation
This is the most important part of Exhaust Lite. Without it you are exhausting with 100% dirty air to outside.

Filter specs
ELG2 filter needs to be filled with activated carbon pellets before being used. Otherwise, it will exhaust with 100% dirty air.
Each filter cartridge requires at least 90g of carbon pellets.

The filter against the carbon dust is recommended. You can make 30x40mm and 30x67mm shield for intake (top-right) and exhaust (left) respectively. You may use new filters. You may need to use the double-sided adhesive to stick the shield to the sides of the unit.

Spec | Minimum | Recommended
Carbon type | 4mm Pellets
Carbon acidity | Neutral (pH 7-9)
Carbon Tetrachloride | 60% or more | 80% or more
Effective area | 600m²/g or over | 1000m²/g or over


Filter cartridge assembly

Carbon dust shield | Carbon pellets 90g or more

Filter shell
filter-shell.stl

Completed filter shell

Filter cartridge top cover filter-cover.stl

4X M2*10mm self-tapping screws

Slotting the filter to the body

Assembled filter cartridge

Body unit


Cover attaching

Unit cover
4X M3*6mm BHCS

Attaching the back Bowden tube

Bowden retainer

Back Bowden tube

Unit body

# Vent port

Preparation
The 6*3mm magnets must attract each other for the vent port to be attached.
If they repel each other, the vent port will never be attached.
The vent port's magnet slot must be coated with or with at least a drop of superglue.

Vent port
ventport-for-elg2.stl

Coat or drop of
superglue

Attracting side


Attaching the hose

Unit body

Vent hose
40-43mm

The securing options may not be shown. You may either use zip-ties or friction-fit to attach.

Vent port

# Software configuration

Some settings for the original exhaust unit can be kept unchanged. However, for the LEDs, you may have to change, or insert if it is connected to the different pin. You may refer to Config/Exhaust Lite for the code and they will be explained. For the runout sensing, you may refer to the dedicated runout.cfg configuration file.

To use ELG2 configuration files conveniently, you can download elg2.cfg and runout.cfg files, then put them into your printer's configuration window and then add [include elg2.cfg] into the base configuration file (mostly printer.cfg) and it should ready to go.

If your printer has never used exhaust fan before, you may try finding exhaust fan config in your base config file and uncomment first. Otherwise, if it is too impossible, you may uncomment that inside elg2.cfg configuration file.

runout.cfg is just a plug-and-play configuration file. If you have installed the coupler adapter that has filament runout sensing, you can uncomment the runout.cfg assignment [include runout.cfg] in elg2.cfg configuration file.

You should change the pin assigned if the board uses pin that is different, like for example BTT Manta M8P, Kraken and Makerbase Monster8.

# Assembly complete

And we are done! If you are satisfied with such product consider tagging @officialbunny350 on Facebook or @realBunny350 on X (formerly known as Twitter) and share such product with us on Oitswilliam Pang Discord Server.

If you have enquires, problems or issues related to building or using such product, please report it on GitHub.com/Bunny350/OITSWILLIAMV2/issues and we will get on it.

See you guys next time!

# Change log

2026-01-24 - Add shadows. Change change log date and time format to the same as the front page. Minor position adjustment on page 11, Fix unknown wire length on pages 12, 13 and 14. Minor adjustments to the front page such as removal of slogan and make mod title bold.
2025-01-04 - Fix misplaced part names
2024-04-12 - Changes to 1/8" BSPP with filament runout detector. Added the second ball bearing in an attempt to address part grinding, especially when used abrasive filament on such weaker part. Add recommended wrench size for coupler.
2024-02-05 - Manual release for ELG2, after many months of wait and finale refresh.

It's done. While you are at my social platforms maybe should you follow me?

Manual designed by Oitswilliam Pang. One-person operated design. www.oitswilliam.com

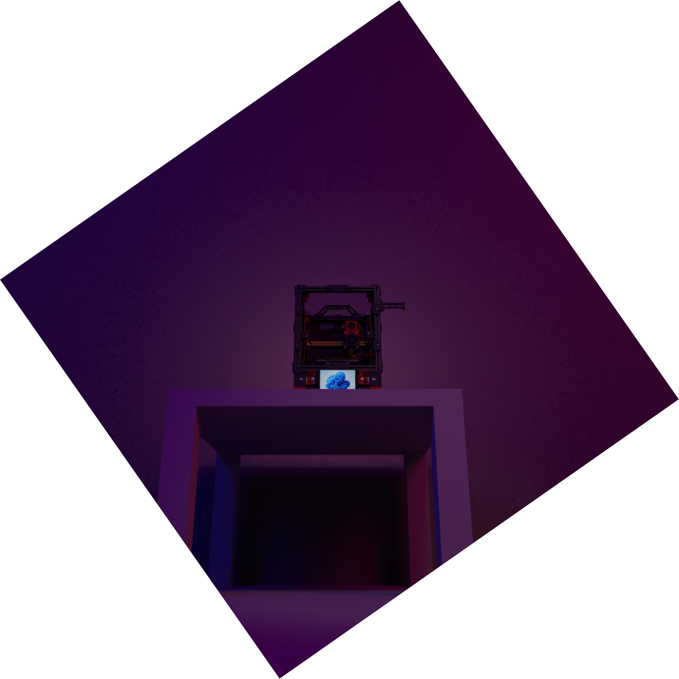
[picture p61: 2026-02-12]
Media/Renders/printer-render-2023.png

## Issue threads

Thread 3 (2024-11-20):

[PSA] [ELG2] Filament grinding

Bunny350, 2024-11-20:
This issue only affects ELG2 with 8/1" BSPP coupler with mechanical switch filament runout sensor.
I was shown that such unit is prone of being ground by filaments over the time, especially when using abrasive materials, which resulted in runout false triggering. When opened for inspection, the path has ground down and left, when looking at the output side.

<!-- 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 -->

The input side:
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

The output side:
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

**Even when the grind is too small to observe, it's enough to throw false positives while printing.**

**This issue may also affect normal Voron 0.2 filament runout sensor.**
## Procedures
1. Add 8/1" BSPP coupler mount with mechanical switch runout sensor to the ELG2 main unit.
2. Collect around 250 hours of print time (or less) (or around 8 spools of filament, the more abrasive the quicker this issue shows and less spools used),
3. The issue becomes prominent as the part gets worn.
## Workaround
The later revision of ELG2 has added the second ball bearing below the first one that is fixed by one M5*20 to 30 BHCS which will address such issue, without the need of new or more durable of printing material. It will become available as soon as after I have checked that it works flawlessly.

Closed 2024-12-04.

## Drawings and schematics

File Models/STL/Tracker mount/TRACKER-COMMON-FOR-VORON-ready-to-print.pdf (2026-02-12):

Brief instructions: • This page should be skipped from being

printed,
- In the print dialog, you may choose which page to print, try avoid printing both versions,
- Page 2 contains the instruction in AirTag version (TRACKER-AIRTAG-FOR-VORON),
- Page 3 contains the instruction in Galaxy SmartTag2 version (TRACKER-SMARTTAG2-FOR-VORON),
- This document uses 4x6" paper size spec. If you have it, use it, otherwise, it needs to be scaled.
- You may prepare a double-sided tape to add adhesive and to convert the paper into a sticker.
- You can use scissors or utility knife to cut the edges out.
- If you have a cutting machine (i.e. Cricut cutting machines or Bambu Lab H2 series), it's recommended that you use the SVG or PNG version.
- If you are importing SVG or PNG, be sure to set its size to 4cm.

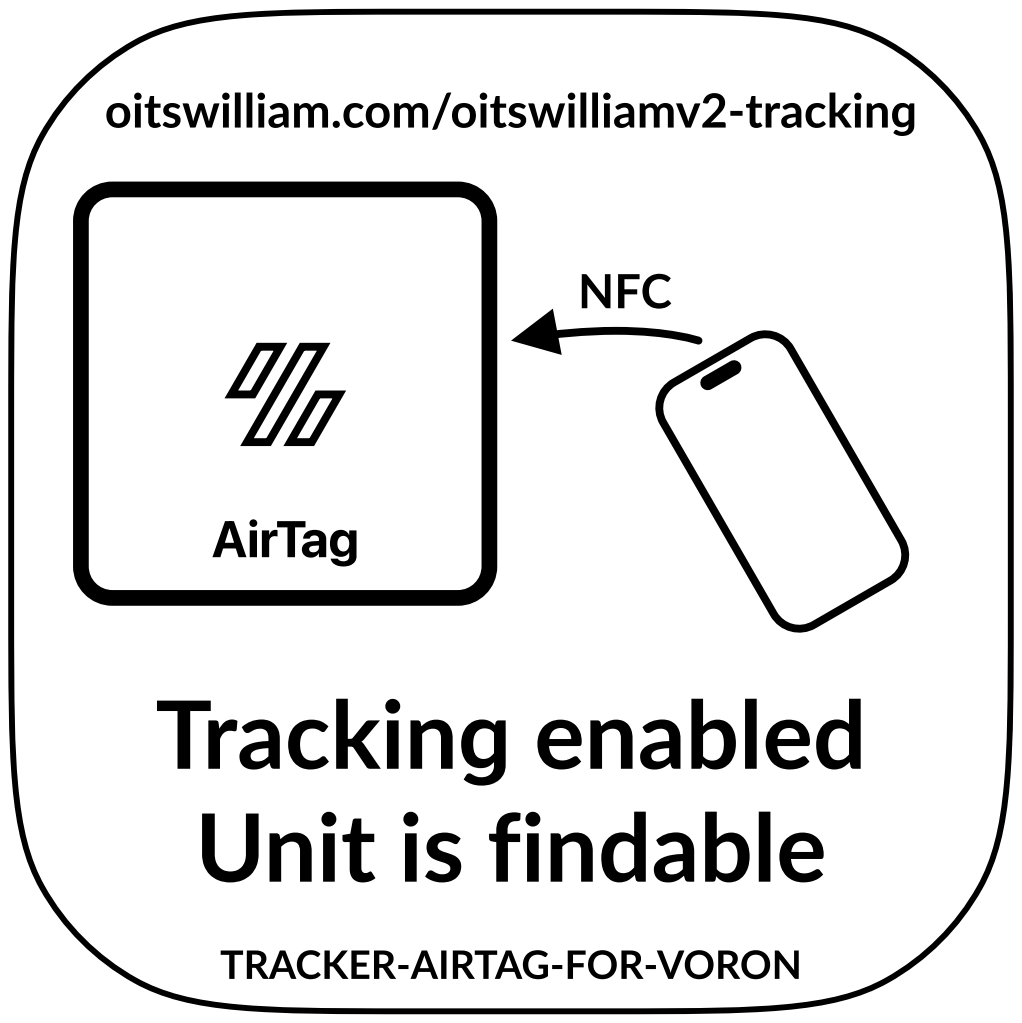
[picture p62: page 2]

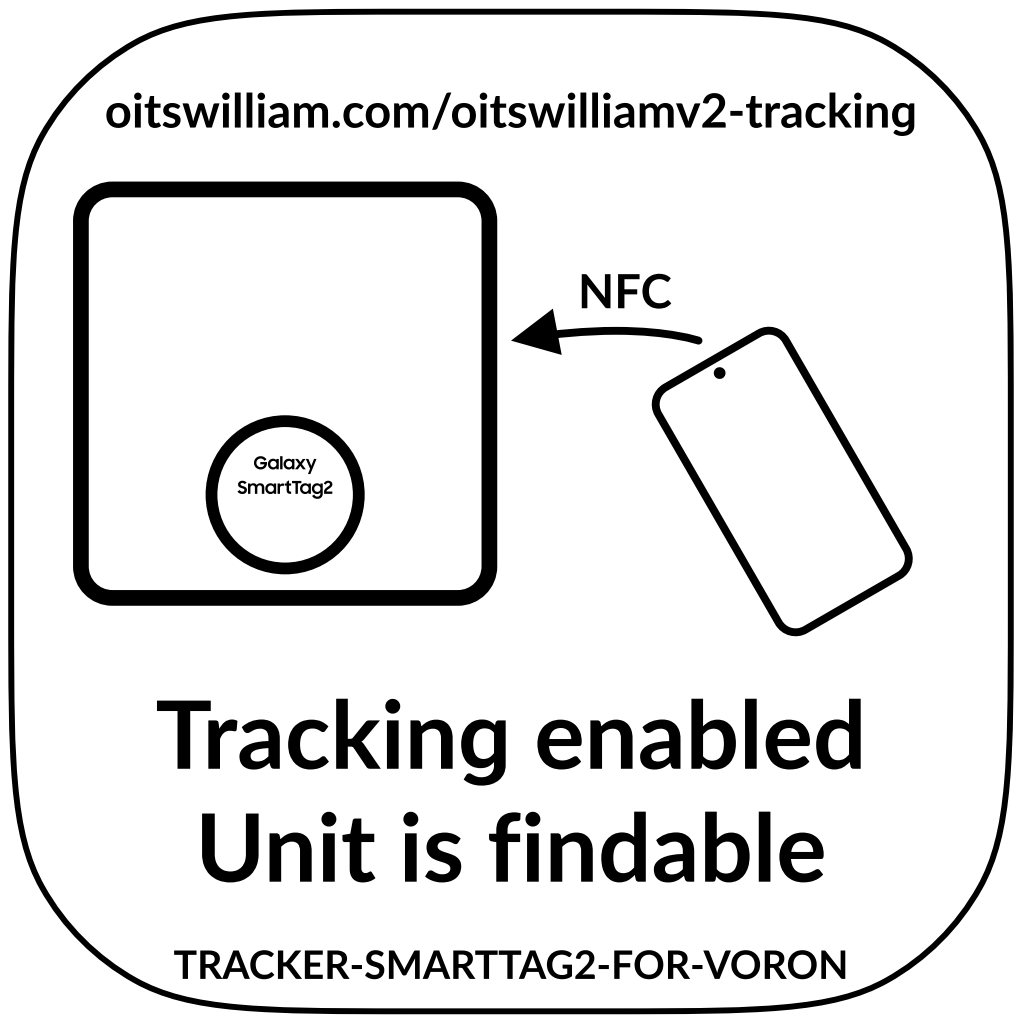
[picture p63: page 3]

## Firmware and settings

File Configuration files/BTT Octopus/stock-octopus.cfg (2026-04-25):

# This file contains common pin mappings for the BigTreeTech OctoPus V1.
# To use this config, the firmware should be compiled for the STM32F446 with a "32KiB bootloader"
# Enable "extra low-level configuration options" and select the "12MHz crystal" as clock reference
# after running "make", copy the generated "klipper/out/klipper.bin" file to a
# file named "firmware.bin" on an SD card and then restart the OctoPus with that SD card.

# See docs/Config_Reference.md for a description of parameters.

# OITSWILLIAMV2 for V2.4 (r1 / r2) + V2.4 150mm + Voron Tap (Klicky or original probe compatible)
# If this config was found for the first time, and you think its config is fully suitable,
# you can copy the whole config and then paste them into printer.cfg file, or just [include stock-octopus.cfg] in your printer.cfg file.
# This config has optional features, configurations or settings that needs additional plugins.
# Klicky probe: https://github.com/jlas1/Klicky-Probe/tree/main/Klipper_macros
# Voron Tap: https://github.com/VoronDesign/Voron-Tap
# OITSWILLIAMV2 mods: https://github.com/Bunny350/OITSWILLIAMV2

## *** THINGS TO CHANGE/CHECK: ***
## MCU paths							[mcu] section
## Thermistor types						[extruder], [heater_bed] and [temperature_sensor] sections - See 'sensor types' list at end of temperature sensors
## Z Endstop Switch location			[safe_z_home] section
## Homing end position				[gcode_macro G32] section
## Z Endstop Switch offset for Z0		[stepper_z] section
## Probe points							[quad_gantry_level] section
## Min & Max gantry corner postions		[quad_gantry_level] section
## PID tune								[extruder] and [heater_bed] sections
## Fine tune E steps					[extruder] section

[mcu]
##	[X in MOTOR0] - B Motor
##	[Y in MOTOR1] - A Motor
##	[E in MOTOR6] - Extruder
##--------------------------------------------------------------------
##	Obtain definition by "ls -l /dev/serial/by-id/" then unplug to verify
##--------------------------------------------------------------------
serial: /dev/serial/by-id/usb-Klipper_stm32f446xx_id_unknown_follow_in_printer_config_file

[temperature_sensor rPi]
sensor_type: temperature_host
min_temp: 10
max_temp: 80

[temperature_sensor MCU]
sensor_type: temperature_mcu
min_temp: 0
max_temp: 65

# Force Move
# Can be commented after comissioning / setup.
[force_move]
enable_force_move: true

[printer]
kinematics: corexy
max_velocity: 700
max_accel: 6000
max_z_velocity: 40
max_z_accel: 350 # 350 for stock V2.4
square_corner_velocity: 5.0

#####################################################################
# 	X/Y Stepper Settings
#####################################################################

## X Stepper on MOTOR0(B Motor)
[stepper_x]
step_pin: PF13
dir_pin: PF12
enable_pin: !PF14
rotation_distance: 40
microsteps: 32
full_steps_per_rotation:200  #set to 400 for 0.9 degree stepper
endstop_pin: PG6
position_min: 0
position_endstop: 150
position_max: 150
homing_speed: 100
homing_retract_dist: 5
homing_positive_dir: true

##	Make sure to update below for your relevant driver (2208 or 2209)
[tmc2209 stepper_x]
uart_pin: PC4
interpolate: true
run_current: 1.2
hold_current: 0.8
sense_resistor: 0.110
stealthchop_threshold: 0

## Y Stepper on MOTOR1 (A Motor)
[stepper_y]
step_pin: PG0
dir_pin: PG1
enable_pin: !PF15
rotation_distance: 40
microsteps: 32
full_steps_per_rotation:200  #set to 400 for 0.9 degree stepper
endstop_pin: PG9
position_min: -2
## 150mm
position_endstop: 155
position_max: 155
homing_speed: 100
homing_retract_dist: 5
homing_positive_dir: true

[tmc2209 stepper_y]
uart_pin: PD11
interpolate: true
run_current: 1.2
hold_current: 0.8
sense_resistor: 0.110
stealthchop_threshold: 0
 
#####################################################################
# 	Z Stepper Settings
#####################################################################

## Z0 Stepper - Front Left on MOTOR2_1
[stepper_z]
step_pin: PF11
dir_pin: PG3
enable_pin: !PG5
rotation_distance: 40
gear_ratio: 80:16
microsteps: 32
endstop_pin: probe:z_virtual_endstop # Change the value to PG10 if not using probe as Z end-stop.
##  Z-position of nozzle (in mm) to z-endstop trigger point relative to print surface (Z0)
##  (+) value = endstop above Z0, (-) value = endstop below
##	Increasing position_endstop brings nozzle closer to the bed
##  After you run Z_ENDSTOP_CALIBRATE, position_endstop will be stored at the very end of your config
# position_endstop: -0.5 # Un-comment if not using probe as Z end-stop.
position_max: 140
position_min: -2 # -1 if it can home or probe in more than 0
homing_speed: 40
second_homing_speed: 8
homing_retract_dist: 5

[tmc2209 stepper_z]
uart_pin: PC6
interpolate: true
run_current: 1.0
hold_current: 0.8
sense_resistor: 0.110
stealthchop_threshold: 0

##	Z1 Stepper - Rear Left on MOTOR3
[stepper_z1]
step_pin: PG4
dir_pin: !PC1
enable_pin: !PA0
rotation_distance: 40
gear_ratio: 80:16
microsteps: 32

[tmc2209 stepper_z1]
uart_pin: PC7
interpolate: true
run_current: 1.0
hold_current: 0.8
sense_resistor: 0.110
stealthchop_threshold: 0

##	Z2 Stepper - Rear Right on MOTOR4
[stepper_z2]
step_pin: PF9
dir_pin: PF10
enable_pin: !PG2
rotation_distance: 40
gear_ratio: 80:16
microsteps: 32

[tmc2209 stepper_z2]
uart_pin: PF2
interpolate: true
run_current: 1.0
hold_current: 0.80
sense_resistor: 0.110
stealthchop_threshold: 0

##	Z3 Stepper - Front Right on MOTOR5
[stepper_z3]
step_pin: PC13
dir_pin: !PF0
enable_pin: !PF1
rotation_distance: 40
gear_ratio: 80:16
microsteps: 32

[tmc2209 stepper_z3]
uart_pin: PE4
interpolate: true
run_current: 1.0
hold_current: 0.80
sense_resistor: 0.110
stealthchop_threshold: 0


#####################################################################
# 	Extruder
#####################################################################

#	E0 on MOTOR6
[extruder]
step_pin: PE2
dir_pin: !PE3
enable_pin: !PD4
##	Update value below when you perform extruder calibration
##	If you ask for 100mm of filament, but in reality it is 98mm:
##	rotation_distance = <previous_rotation_distance> * <actual_extrude_distance> / 100
##  22.6789511 is a good starting point
rotation_distance: 22.23	# Clockwork 2, Bondtech 5mm Drive Gears
##	Update Gear Ratio depending on your Extruder Type
##	Use 50:17 for Afterburner/Clockwork (BMG Gear Ratio)
##	Use 80:20 for M4, M3.1
##  Use 15:2 for Galileo Clockwork by JaredC01
gear_ratio: 50:10				# Clockwork 2 main by motor gear ratio
microsteps: 32
full_steps_per_rotation: 200	#200 for 1.8 degree, 400 for 0.9 degrees
nozzle_diameter: 0.400
filament_diameter: 1.75
heater_pin: PA2
##	Validate the following thermistor type to make sure it is correct
sensor_type: ATC Semitec 104GT-2
sensor_pin: PF4
min_temp: 10
max_temp: 270
max_power: 1.0
min_extrude_temp: 170
## 24V50W
control = pid
pid_kp = 24.964
pid_ki = 1.331
pid_kd = 117.019
##	Try to keep pressure_advance below 1.0
pressure_advance: 0.05
##	Default is 0.040, leave stock
pressure_advance_smooth_time: 0.040

##	E0 on MOTOR6
[tmc2209 extruder]
uart_pin: PE1
interpolate: false
run_current: 0.35	# reduce overheating, set to 0.5 for default config
hold_current: 0.2	# reduce overheating
sense_resistor: 0.110
stealthchop_threshold: 0


#####################################################################
# 	Bed Heater
#####################################################################

[heater_bed]
##	In Voron GitHub source code https://github.com/VoronDesign/Voron-2/blob/Voron2.4/firmware/klipper_configurations/Octopus/Voron2_Octopus_Config.cfg
##	HE1 is the recommended SSR control pin, however making this printer mobile will render the bed heater useless.
##	If the printer uses DC heated bed (or former SSR pin) then it should not be changed.
heater_pin: PA1	## DC heated bed
sensor_type: Generic 3950
sensor_pin: PF3
##	Adjust Max Power so your heater doesn't warp your bed
max_power: 1.0	# DC 24V 100W ; set to 0.6 if the output is more than 0.4W per cm^2.
min_temp: 0
max_temp: 125
# pwm_cycle_time: # For 50Hz (PAL) AC SSR, set it to 0.02, but for 60Hz (NTSC), set it to 0.0166. DC does not require that. Sourced from NERO 3D's video.
## DC 24V 100W
control: pid
pid_kp = 56.981
pid_ki = 1.751
pid_kd = 463.684

#####################################################################
# 	Other temperature sensors
#####################################################################

# chamber sensor
# Un-set by commenting using # at the beginning of this line if not installed.
[temperature_sensor chamber]
sensor_type: Generic 3950
sensor_pin: PF5
max_temp: 75 # Max temperature before shut-down. Do not remove or comment this!!! Please increase if you have caught unwanted triggers.
# End

## Environment temperature sensor
## Experimental feature, adds additional safety and peace-of-mind.
# [temperature_sensor environment-temperature]
# sensor_type: Generic 3950
# sensor_pin: PF6
# max_temp: 50
## End
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

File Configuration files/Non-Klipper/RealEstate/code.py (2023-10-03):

import time
from digitalio import DigitalInOut, Direction, Pull
import board
import usb_hid
from adafruit_hid.consumer_control import ConsumerControl
from adafruit_hid.consumer_control_code import ConsumerControlCode

print ("waking")

# USB device
consumer = ConsumerControl(usb_hid.devices)

pinns = (
    board.GP9,
    board.GP8,
    board.GP7
    )

keys = {
    (0): (ConsumerControlCode.VOLUME_INCREMENT),
    (1): (ConsumerControlCode.VOLUME_DECREMENT),
    (2): (ConsumerControlCode.MUTE)
    }
altkeys = {
    (0): (ConsumerControlCode.BRIGHTNESS_INCREMENT),
    (1): (ConsumerControlCode.BRIGHTNESS_DECREMENT),
    (2): ()
    }

button = []
for i in range(len(pinns)):
    buttona = DigitalInOut(pinns[i])
    buttona.direction = Direction.INPUT
    buttona.pull = Pull.UP
    button.append(buttona)
    
keies = [0, 0, 0]

ispressingmute = 0
ispressingbright = 0
brightnessmode = 0
disengaging = 0

# loop
while True:
    for buttonb in range(2):
        if ispressingmute == 0 and disengaging == 0:
            if keies[buttonb] == 0:
                if not button[buttonb].value:
                    try:
                        consumer.press(keys[buttonb])
                    except ValueError:  # deals w six key limit
                        pass
                    keies[buttonb] = 1
                
            if keies[buttonb] == 1:
                if button[buttonb].value:
                    if brightnessmode == 0 and disengaging == 0:
                        try:
                            consumer.send(keys[buttonb])
                        except ValueError:
                            pass
                        keies[buttonb] = 0
                    elif disengaging == 1:
                        disengaging = 0
                    # end of volume mode
        elif ispressingmute == 0 and disengaging == 1 and ispressingbright == 0:
            print("ERR", brightnessmode, ispressingmute, disengaging, ispressingbright)
            disengaging = 0
        if ispressingmute == 1:
            if keies[buttonb] == 0:
                if not button[buttonb].value:
                    brightnessmode = 1
                    ispressingbright = 1
                    print ("brightnessmode engaged!1")
                    if brightnessmode == 1:
                        try:
                            consumer.press(altkeys[buttonb])
                        except ValueError:  # deals w six key limit
                            pass
                        keies[buttonb] = 1
                
            if keies[buttonb] == 1:
                if button[buttonb].value:
                    ispressingbright = 0
                    try:
                        consumer.send(altkeys[buttonb])
                    except ValueError:
                        pass
                    keies[buttonb] = 0
        elif disengaging == 1:
            if keies[buttonb] == 1:
                if button[buttonb].value:
                    print ("prepare to disengage in the second way")
                    try:
                        consumer.send(altkeys[buttonb])
                    except ValueError:
                        pass
                    keies[buttonb] = 0
                    disengaging = 0
                # end line of brightness mode
    for buttonC in range(1):
            if keies[buttonC + 2] == 0:
                if not button[buttonC + 2].value:
                    ispressingmute = 1
                    try:
                        if keies[buttonC + 2] == 0 and ispressingmute == 1:
                            print ("mute pressed")
                    except ValueError:  # deals w six key limit
                        pass
                    keies[buttonC + 2] = 1
                
            if keies[buttonC + 2] == 1:
                if button[buttonC + 2].value:
                    try:
                        if brightnessmode == 0:
                            consumer.send(keys[buttonC + 2])
                            print("mute switch mode")
                        else:
                            brightnessmode = 0
                            disengaging = 1
                            print ("disengaging", disengaging)
                            print ("brightnessmode disengaged")
                    except ValueError:
                        pass
                    ispressingmute = 0
                    keies[buttonC + 2] = 0
    time.sleep(0.01)

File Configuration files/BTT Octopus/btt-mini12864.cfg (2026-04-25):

[display]
##	mini12864 LCD Display
lcd_type: uc1701
cs_pin: EXP1_3
a0_pin: EXP1_4
rst_pin: EXP1_5
encoder_pins: ^EXP2_5, ^EXP2_3
click_pin: ^!EXP1_2
contrast: 63
spi_software_miso_pin: EXP2_1
spi_software_mosi_pin: EXP2_6
spi_software_sclk_pin: EXP2_2

[neopixel btt_mini12864]
##	To control Neopixel RGB in mini12864 display
pin: EXP1_6
chain_count: 3
initial_RED: 0.5
initial_GREEN: 0.5
initial_BLUE: 0.32
color_order: RGB

##	Beeper PWM fix
[output_pin beeper]
pin: EXP1_1
pwm: true
cycle_time: 0.000365

##	Set RGB values on boot up for each Neopixel. 
##	Index 1 = display, Index 2 and 3 = Knob
# [delayed_gcode setdisplayneopixel]
# initial_duration: 1
# gcode:
#        SET_LED LED=btt_mini12864 RED=1 GREEN=1 BLUE=1 INDEX=1 TRANSMIT=0
#        SET_LED LED=btt_mini12864 RED=1 GREEN=0 BLUE=0 INDEX=2 TRANSMIT=0
#        SET_LED LED=btt_mini12864 RED=1 GREEN=0 BLUE=0 INDEX=3 

#####################################################################
- Supplemental menu features
#####################################################################

[menu __main __octoprint]    # New Voron printers use lightweight interface (i.e. Mainsail and fluidd)
type: disabled

[menu __main __control __aga]   # QGL via G32
type: command
enable: {not printer.idle_timeout.state == "Printing"}
name: Align gantry G32
gcode: G32

 [menu __main __shutdown]    # Shutdown through display
    type: command
    enable: {printer.idle_timeout.state != "Printing"}
    name: Shutdown
    gcode:
    {% if printer.idle_timeout.state != "Printing" %}
    SET_LED LED=btt_mini12864 RED=0.0 GREEN=0.0 BLUE=0.0
    {action_call_remote_method("shutdown_machine")}
    {% endif %}
    

## Classic dim and invoke macros
[gcode_macro DIM] # Classic dim (used during print)
description: Classic dim
gcode:
    SET_LED LED=btt_mini12864 RED=0.05 GREEN=0.05 BLUE=0.02

[gcode_macro INVOKE] #Classic invoke (used during pause, cancel or complete)
description: Classic invoke
gcode:
    SET_LED LED=btt_mini12864 RED=0.5 GREEN=0.5 BLUE=0.32

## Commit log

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2022-11-02 Additions and removals
    Add RealEstate display, add panel mount skirt and remove direct attach USB port ones
    [[righthand]usb-port-2x.stl, [righthand]usb-port-camera.stl, [transparent]led-diffuser.stl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]
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2022-11-27 RealEstate G2
    The most advanced tiltable display unit just got more insane
    Currently in Early Access stage
    [60mm-Fan-mount-150mm-mod.step, [acc]airtag-trackermount-g3.stl, [acc]fangrill-condensed.stl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]
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2022-12-29 New update
    Back assembly: move USB ports up
    Hatches: add fillet for better design and printability
    Middle hub: add logo
    main-screen-mount-waveshare-5.5-inch-amoled: thickened the border
    [back-assembly-screw-based-panel-mount.stl, hatch (for default endstop).stl, hatch.stl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]
2023-03-01 Minor updates
    * Fix offset on back assembly mount holes
    * Minor changes in hatches and middle hub
    [back-assembly-screw-based-panel-mount.stl, hatch (for default endstop).stl, hatch.stl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]
2023-03-06 Add remaining hardware parts on CAD
    Beside this the tilt pump also has a reflection change
    [tilt-bump.stl]
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2023-04-05 Re-add past files to prepare pushing as official release
    This change also updates the manual to specify more information about wiring and lever removal needs for printer end stop power switch
    [60mm-Fan-mount-150mm-mod.step, [acc]airtag-trackermount-g3.stl, [acc]fangrill-condensed.stl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]
2023-06-08 ELG2 EA
    This time I will not be releasing the CAD until when the assembly manual is going to be made. This mod is currently unstable and there could be model changes done quickly.
    [8-1-bspp-adapter.stl, [base]exhaust-body-OITSWILLIAMV2.stl, [base]exhaust-body-cover.stl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]
2023-07-07 New part and changes
    * Removal of dedicated fan connector on the main unit and hose mount unit, due to difficulties in assembly and use
    * Add print LED unit
    [[transparent]print-led-diffuser.stl, main-body.stl, print-led-unit.stl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]
2023-07-14 Update realestate-generation-2-assembly-guide.pdf
    * Fix words.
    * Fix (intentional) spelling issues. Rename heat seats to heat sets.
2023-07-27 Minor changes
    This fixes user-design error on all wire guides and punching down the remaining top holes.
    [[opaque]led-mount-lefthand.stl, [opaque]led-mount-righthand.stl, wire-guide-unified-10MM.stl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]
2023-08-15 Config changes and add new parts
    * Reduce LED from 34 to 30.
    * some changes in BTT Octopus config file
    * Add 8/1 BSPP adapter with runout endstop for ELG2
    [8-1-bspp-adap-runout.stl, flying-color.cfg, stock-octopus.cfg]
2023-09-10 Add 6MM parts and a forgotten part, among other changes
    This adds a new config file for the newly adopted Bowden coupler, 6mm thickness version of parts and a forgotten part led-wire-exhaust-spacer-4mm.
    [8-1-bspp-adap-runout.stl, [transparent]diffuser-lefthand-6mm.stl, [transparent]diffuser-lefthand.stl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]
2023-10-03 RealEstate Generation 2.1
    RealEstate G2.1 is a minor upgrade of RealEstate G2 that adds volume and mute or print and E-stop button, depending on how you use them to the hatch of the display. A new version of assembly manual adds wiring guides for G2.1 hatch. G2.1 hatch works with G2 display mounts which are unchanged.
    This also removes G1 components which is no longer maintained after G2.
    This also changes the logo for the whole mod project and move RealEstate STLs models away from models parent folder.
    [[transparent]humor-bar-led-diffuser.stl, back-assembly-screw-based-panel-mount.stl, button.stl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]
2024-05-20 Model refresh and hopping to RC
    This change finally added the damn assembly manual after my laziness!!!
    Among other things, I decide to deprecate PTP feature and RepRapDiscount display modular config.
    Some files are reorganized for better findings and added a dedicated directory guide for printing.
    [8-1-bspp-adap-runout.stl, [opaque]led-mount-lefthand.stl, [transparent]chamber-led-diffuser.stl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]
2024-05-26 Update realestate-generation-2-1-assembly-guide.pdf
    This minor update replaces the former link to the new link with self-created domain.
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2024-12-04 [8-1-bspp-adap-runout] Filament grinding fix
    This change fixes one of the problem that lead to permanent damage and false-triggering due to grinding by sliding filament.
    By addressing this we added:
    * an additional ball bearing,
    * an additional M5*30 screw.
    The CAD for ELG2 is updated and the BOM has added the materials for such coupler mount with filament runout detector, and is now the recommended config.
    Beside this the release status for ELG2 in root readme page has changed from EA to GA, I forgot about this during the official release of it.
    [8-1-bspp-adap-runout.stl, exhaust-lite-gen2 v37.f3d, exhaust-lite-gen2 v37.step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]
2024-12-04 Change from 8/1" to 1/8" in change log in assembly manual
    The biggest screwup I've ever made© I forgot to change one part of the manual that showed in the wrong dimension.
2026-01-02 Major upgrades
    This update adds NUC mounts and puts SBC-specific parts into respective folder, adds independent tracker CAD files, adds tracker mount for Galaxy SmartTag2, file organization and reorganization and u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
    [60mm-Fan-mount-150mm-mod.f3d, 60mm-Fan-mount-150mm-mod.step, [acc]fan-mount-converter-smarttag.stl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]
2026-01-07 Banger speaker skirts assembly guide release
    Among this, this also adjusts the placements of the speaker unit skirts, adds PrusaSlicer-specific 3MF files and updates RealEstate 2 display to Oitswilliam spec.
    [left side skirt infill mesh modifier.stl, realestate 2 v24.f3d, realestate 2 v24.step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]
2026-01-15 Adjustments
    This change renames the hatch that "has default endstop" to the proper name (hatch-normal-microswitch), updates to RealEstate G2.1 assembly guide to include printable part file names among other things (for more, see change log inside the assembly guide) and adds new question about how powerful the mod is. This change also adds a quick link to Oitswilliam's support page when reporting issues privately without vendors knowing.
    [hatch-normal-microswitch.stl]
2026-01-24 Banger Speakers officially released
    Among this, which included changes to the manual and pre-orientating the models, there are other changes included:
    * Re-add side skirts with mesh on cutouts.
    * Adjusted NUC skirts and renamed some printable parts as NUC 16 Pro will not fit in this skirt.
    * Pre-orient NUC skirt models.
    * Add Readme Markdown file for the full model and the side skirt models print guide.
    * Add Parts printing Markdown file, just because (why not).
    * To reduce storage occupation for the users, the parametric history for tracker mounts and Exhaust Lite Gen2 are removed.
    * Certain wire lengths for ELG2 back LED are now known.
    * Logo materials (from Media folder) are now sorted by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
    [[acc]lock-notch-airtag-mount.stl, [base]bottom-panel.stl, back_skirt_nuc_12to15_pro_left_xt60_power.stl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]
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2026-02-12 Next generation of tracker mounts
    This change introduces the generation 4 of AirTag mount and generation 2 of Galaxy SmartTag2 mount. They both now only require four heat set inserts, four M3*6mm BHCS and three parts.
    For AirTag mount, the delicate alignment notch has been removed. Besides this, there are minor changes to the NUC skirt assembly manual, adjustments to renders media folder and the repository overall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
    [[acc]airtag-trackermount-g3.stl, [acc]fan-mount-converter-smarttag.stl, [acc]front-mount-plate-smarttag.stl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]
2026-02-14 Tracker mounts orientation adjustment
    This change adjusts AirTag and Galaxy SmartTag2 mount orientation, adds notice on when Morefine M6 mount will be removed.
    [[acc]tracker-mount-airtag-back-g4.stl, [acc]tracker-mount-airtag-bracket.stl, [acc]tracker-mount-smarttag-back-g2.stl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]
2026-02-15 Minor fix - spelling change to tracker mount assembly manual
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2026-02-24 Tracker mounts of 2026 released
    This change officially marks AirTag tracker mount G4 and Galaxy SmartTag2 tracker mount G2 in released state, not only that:
    * Updated full model to have AirTag tracker mount G4 (from G3) and minor adjustment to the reverse Bowden tube.
    * Removed AirTag tracker mount G3 in fan mount CAD.
    * Adjusted the lefthand side of the SBC-specific skirt to not have the PCB-based USB port, and added its CAD model.
    * Adjust wordings in the contributing document.
    [60mm-Fan-mount-150mm-mod.f3d, 60mm-Fan-mount-150mm-mod.step, [lefthand]power-inlet-dc-xt60-sbc.f3d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]
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2026-03-05 Minor adjustment - rename studs for NUC 12-15 Pro to explicitly say
    This also renames the NUC-specific skirt from "from 14 Pro" to "from 12 Pro" in Readme document. The CAD file for the NUC skirt will have names remain unchanged until either model change or official 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
    [reinforcement_stud_bottom_nuc12to15pro.stl, reinforcement_stud_top_left_nuc12to15pro.stl, reinforcement_stud_top_right_nuc12to15pro.stl]
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2026-03-24 Update configuration files and remove dated materials
    This removes flying-color.cfg which was belonged to the first generation of Exhaust Lite with its back LED. This also optimizes configuration code, including:
    * Rename "Config" folder to Configuration files.
    * Removed deprecated file links in current configuration files.
    * QGL and probing off set and now uses Voron Tap by default,
    * Increased maximum speed from 600 to 700,
    * Increased acceleration from 4000 to 6000,
    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
    [btt-mini12864.cfg, elg2.cfg, flying-color.cfg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]
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
